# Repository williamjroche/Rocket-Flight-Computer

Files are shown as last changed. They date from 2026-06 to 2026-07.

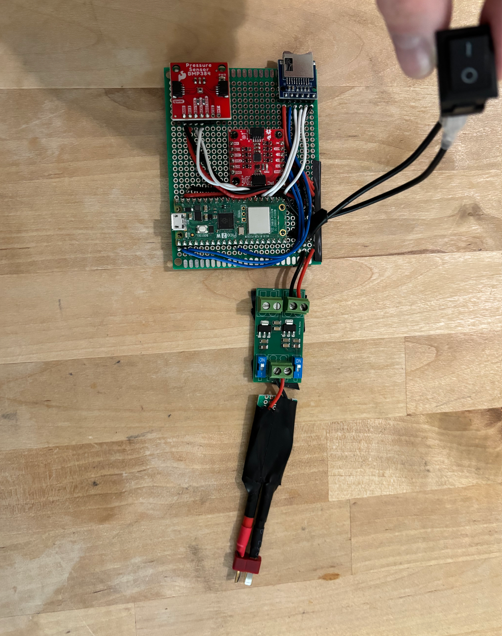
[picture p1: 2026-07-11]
prototype_pictures/photo3.png

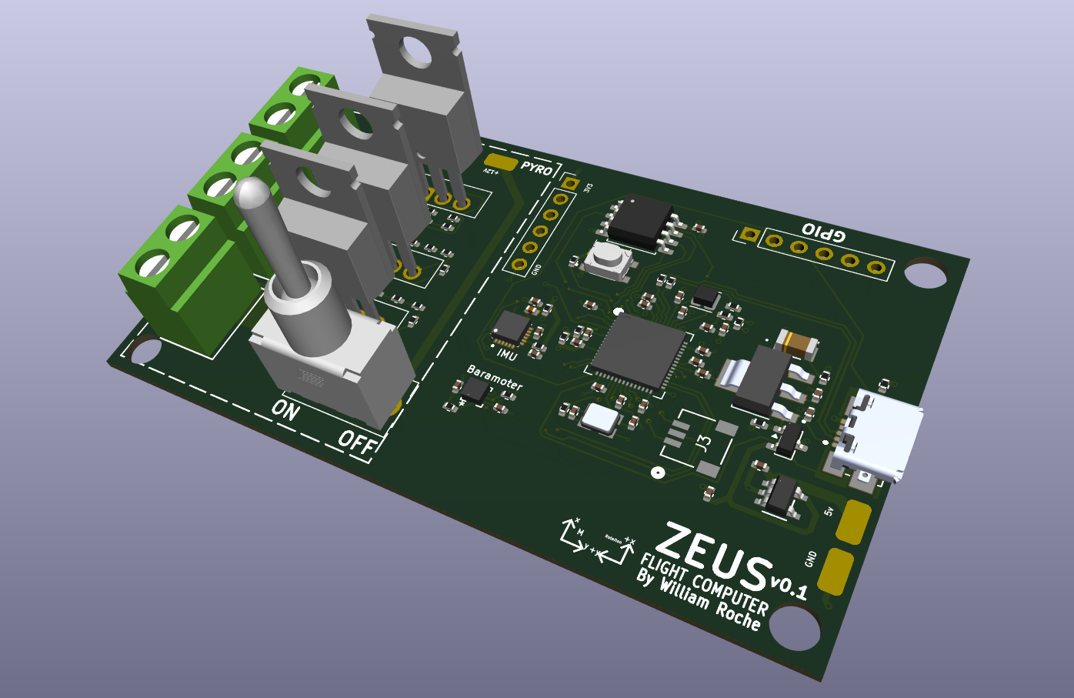
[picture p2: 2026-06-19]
PCB Photos/zeus_3d.png

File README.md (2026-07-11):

# Zeus Flight Computer

Custom flight computer for amature rockets, code named Zeus. This FC records flight data, detects apogee using a 9-axis IMU + baraomter sensor, has a built in pyro circut for firing e-matches (parachute, stage seperation, etc.).

## Project Status

- PCB design in the works, based on my Atlas Flight Controller from this project: https://github.com/williamjroche/Autonomous_drone
- Prototyping in progress on protoboard
- Board not yet fabricated, working on completing prototype first to test architecture

## Features

- 3 pyro channels with continuity sensing
- IMU + barometer sensors for apogee detection
- microSD card reader for data logging
- Automatic USB / external battery power switching (using PMOS switching circuit)
- MicroPython firmware (adapted from drone flight controller project)

## Hardware Overview

- Check out my system diagrams: [System Drawings](./System%20Drawings)
    - Explains architecture at a top level overview
- Key components table (MCU, IMU, barometer, flash, SD, pyro MOSFETs, power management)
- Link to schematic/PCB files [Zeus_FC_PCB](./Zeus_FC_PCB)

## PCB



- Stackup summary (4-layer: signal / GND / 3.3V / signal)
- Check out other photos [PCB Photos](./PCB%20Photos)
- Note: working on finding smaller SMD type IRFZ44N mosfets because these are ugly

## Protoboard Prototype

- Purpose: validate firmware and circuit behavior ahead of PCB fabrication
- Hardware used (Pico 2W, IMU breakout (ICM-20948), barometer breakout (BPM 384), microSD breakout, custom designed and fabricated 12v to 3.3v regulator board)
- Photos coming soon

## Firmware

- project specific firmware not yet developed, coming soon
- Firmware will be based off of Atlas FC firmware: https://github.com/williamjroche/Autonomous_drone/tree/main/flight_controller

## Wiring / Pinout

- Micro SD card reader:
  - CS – GPIO8
  - MISO – GPIO16
  - SCK – GPIO18
  - MOSI – GPIO19
- IMU Board:
  - SDA – GPIO0
  - SCL – GPIO1
- Barometer:
  - SDA: GPIO20
  - SCL: GPIO21

## Getting Started / Prototype Setup

If you want to make your own prototype, you'll need the following materials:

- protoboard, decently sized (mine is 7cm x 9cm)
- soldering iron
- solder (I recommend lead free)
- Fume extractor
- something to clean the soldering iron tip, like steel wool)
- 22awg wire
- Toggle switches (2)
- 1 3s LiPO battery
- Something to convert the 11.1v LiPO battery to 3.3v for the Pi
    - A buck converter off amazon will work
    - or you can download the files from the device I built from here: (https://github.com/williamjroche/Autonomous_drone/tree/main/dual_power_supply)
        - Can be fabricated using PCBway, JLCPCB, or any of your favorite fabricators. I ordered from PCBway.
- Raspberry Pi Pico 2W
- ICM-20948 IMU breakout
- BPM 384 barometer breakout
- Any microSD card reader breakout
- Electrical tape or hot glue
- MicroSD card
- Flux to make soldering easier
- Multimeter to test electrical connections (not needed but helpful)

## My Prototype: 



Here is a demo video of the working prototype: https://youtube.com/shorts/D4aav9IAWUg?si=ib71gM45oc4MuGbN

At the moment only the IMU is programmed, I need to work on the barometer sensor and apogee detection + saving data to micro SD card. You can see in the video I am using my custom dual power PCB I designed which is converting the 12v from the battery to a usable 3.3v for our sensors and Pico 2W. The switch you see is me prototyping a power switch.

## Safety Notes

- Be careful handling pyro charges!
      - I am not responible for any accidents.

## Acknowledgments

- Link to drone flight controller project: https://github.com/williamjroche/Autonomous_drone/tree/main
    - Dual Power Supply PCB is the 12v to 3.3v converter I am using on this project. The explaination under this other repo readme will help clear up any   confusion.

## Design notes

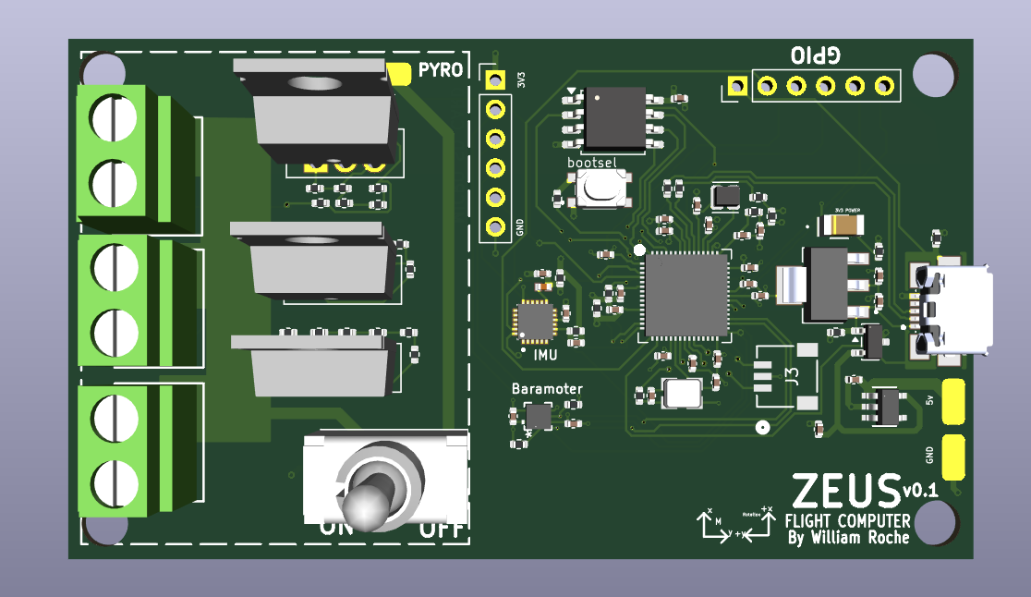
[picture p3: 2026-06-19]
PCB Photos/zeus_3d_top.png

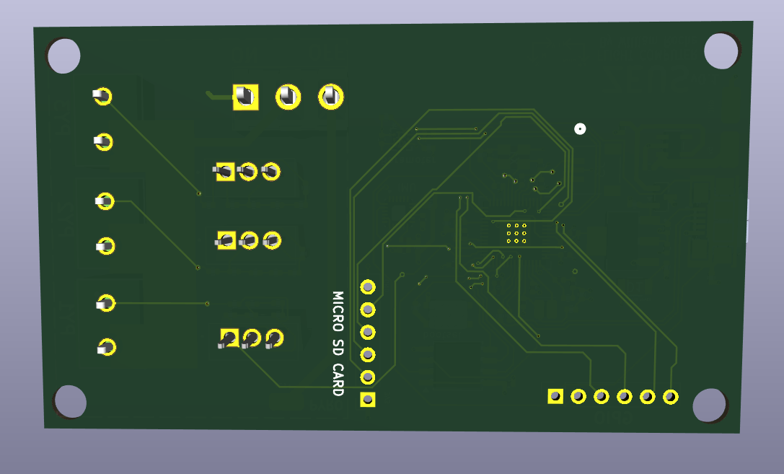
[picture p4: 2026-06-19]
PCB Photos/zeus_3d_bottom.png

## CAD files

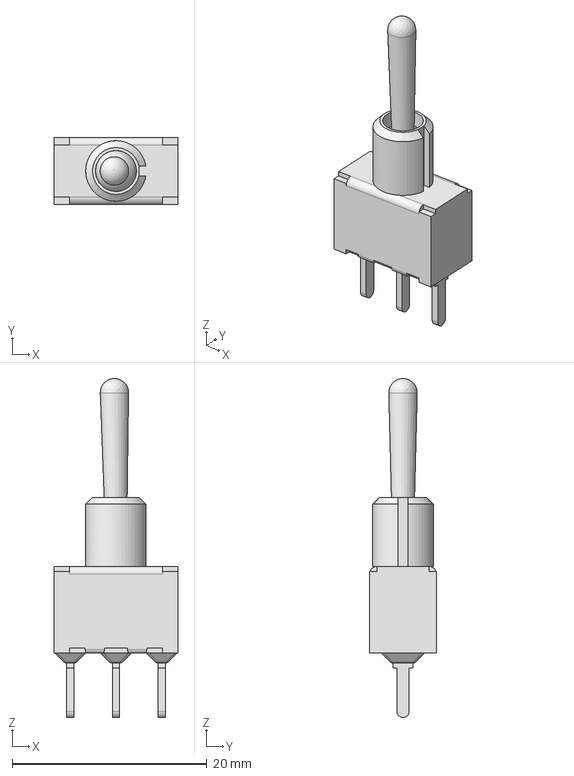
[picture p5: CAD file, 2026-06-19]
Zeus_FC_PCB/100SP1T1B4M2QE/100SP1T1B4M2QE.step
12.7 x 6.86 x 34.8 mm

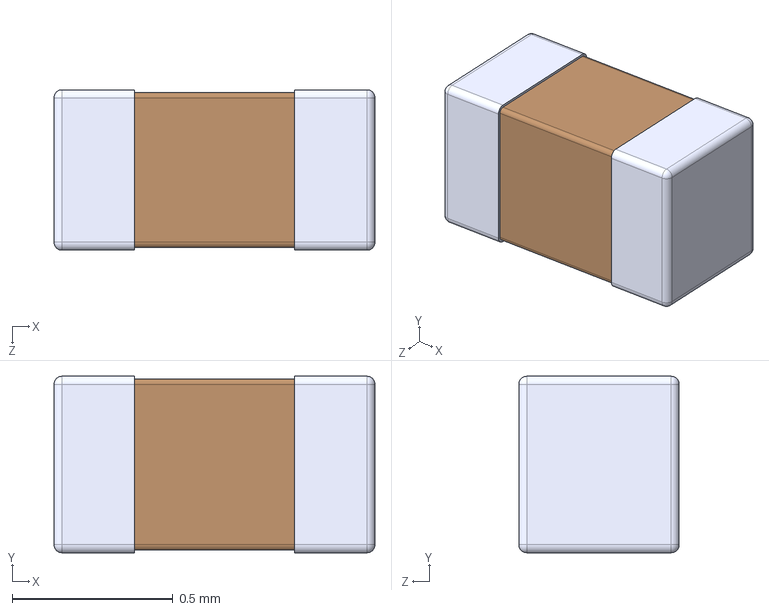
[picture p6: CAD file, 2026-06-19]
Zeus_FC_PCB/BLM15AX601SN1D/BLM15AX601SN1D.step
1.00 x 0.55 x 0.5 mm

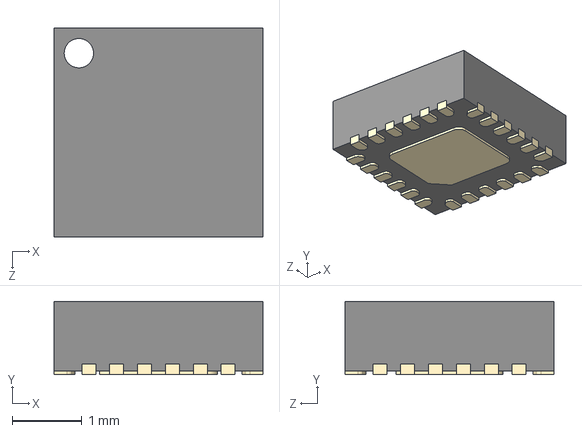
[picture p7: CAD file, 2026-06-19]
Zeus_FC_PCB/ICM-20948/ICM-20948.step
3.00 x 1.05 x 3.00 mm

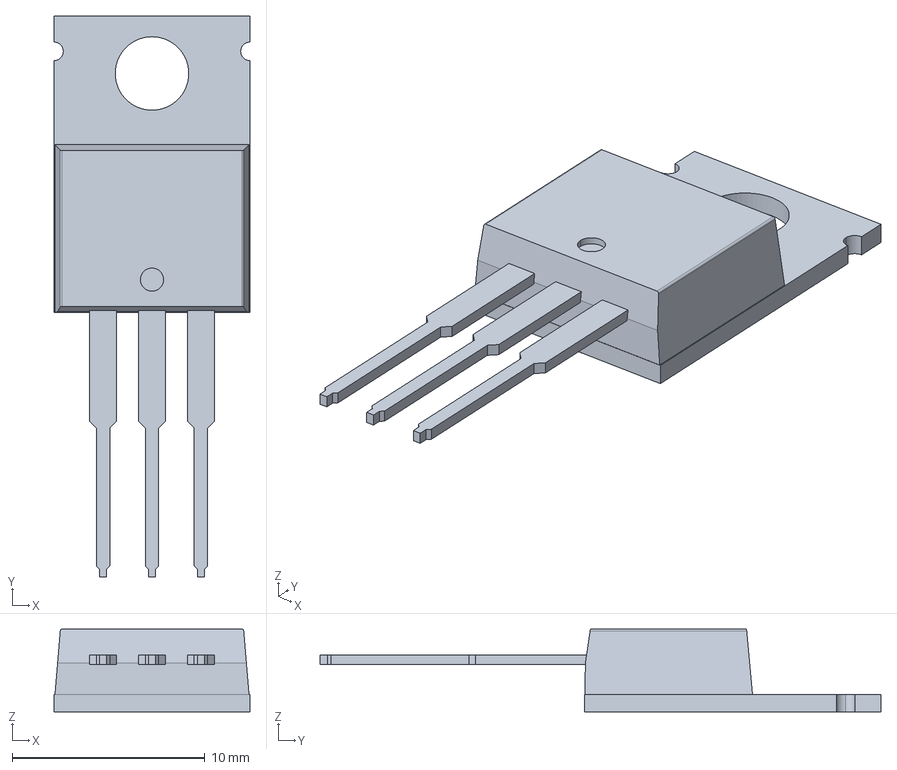
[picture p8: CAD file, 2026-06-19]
Zeus_FC_PCB/IRFZ44NPBF/irfz44npbf.stp
10.2 x 29.1 x 4.30 mm

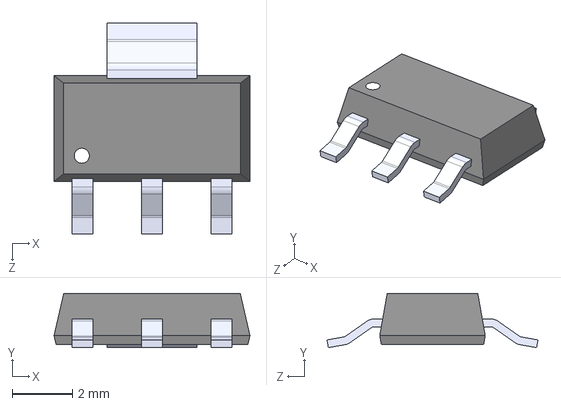
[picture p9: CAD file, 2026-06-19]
Zeus_FC_PCB/LD1117S33TR/LD1117S33TR.step
6.50 x 1.80 x 7.00 mm

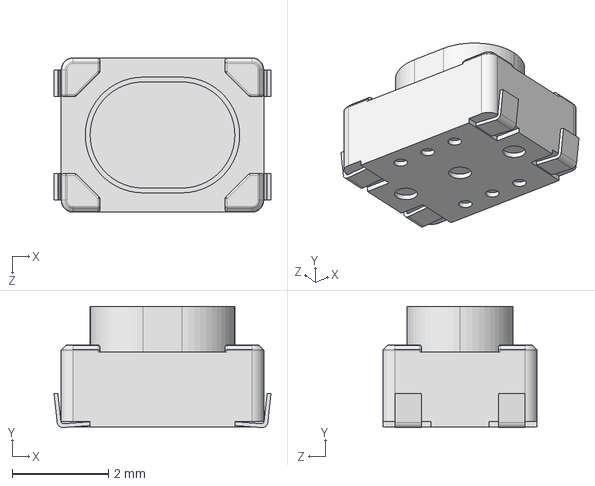
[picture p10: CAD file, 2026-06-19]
Zeus_FC_PCB/TL3365AF180QG/TL3365AF180QG.step
4.50 x 2.51 x 3.20 mm

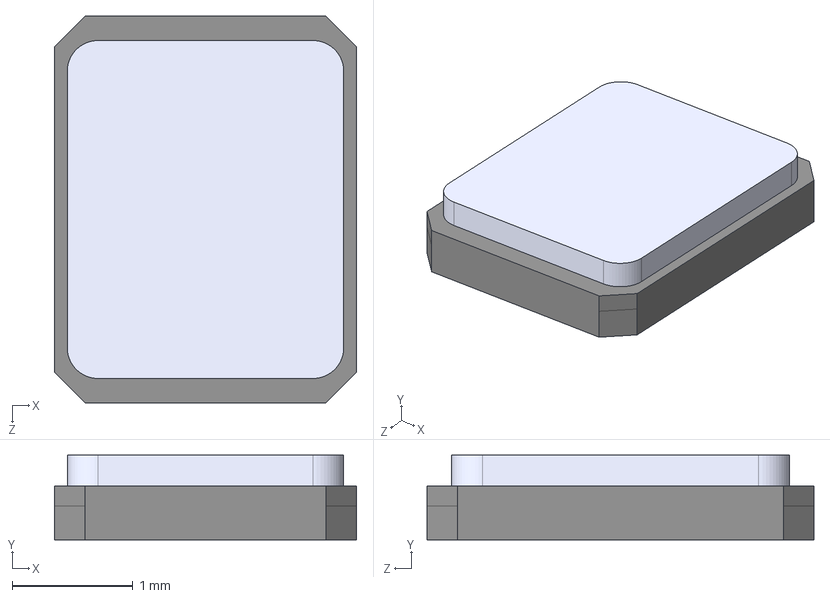
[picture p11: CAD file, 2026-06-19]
Zeus_FC_PCB/ul_ABM8-272-T3/ABM8-272-T3.STEP
2.50 x 0.7 x 3.20 mm

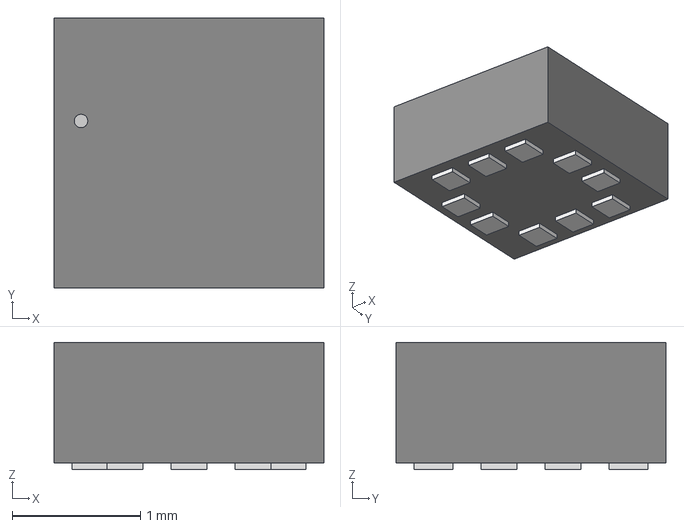
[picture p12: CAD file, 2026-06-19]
Zeus_FC_PCB/ul_BMP384/LGA10_2_0X2_0X0_95_BOS.step
2.11 x 2.11 x 0.993 mm

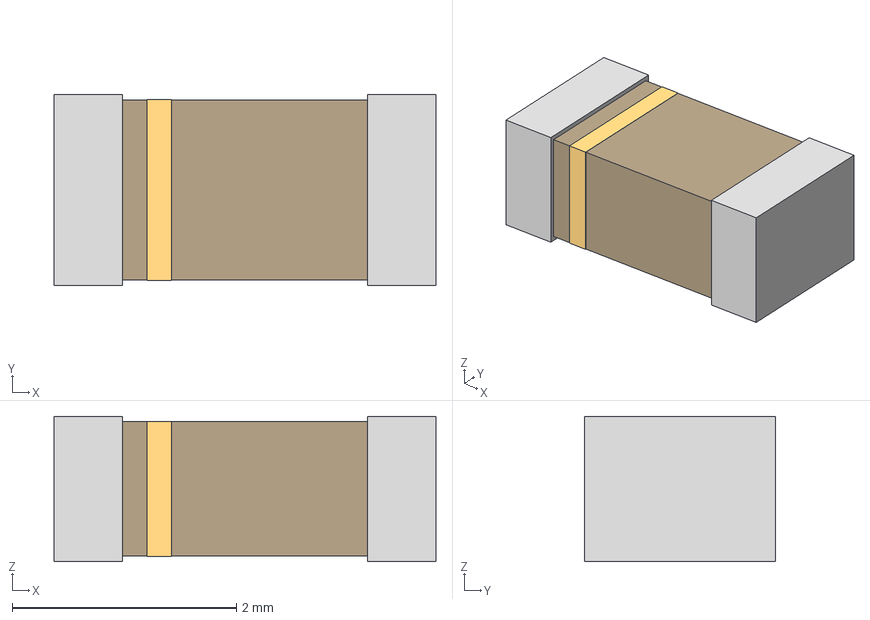
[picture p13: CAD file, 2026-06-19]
Zeus_FC_PCB/ul_CMD15-21VGD-TR8/LED_CMD15-21_VCC.step
3.40 x 1.70 x 1.29 mm

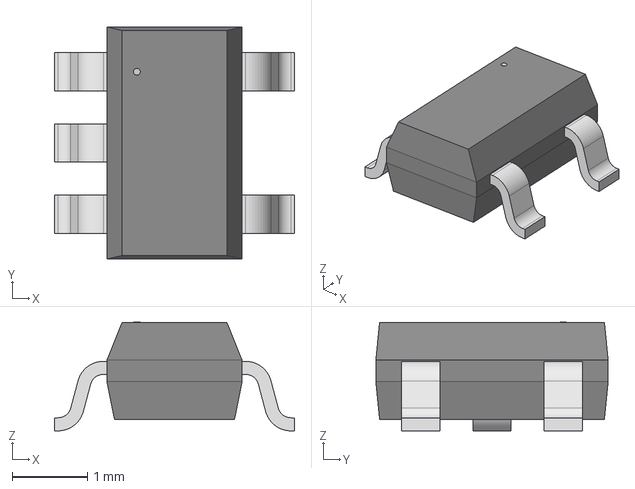
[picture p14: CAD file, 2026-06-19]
Zeus_FC_PCB/ul_MIC5504-3-3YM5-TR/KiCADv6/ul_MIC5504-3-3YM5-TR (1)/SOT-23-5_MC_MCH.step
3.20 x 3.10 x 1.45 mm

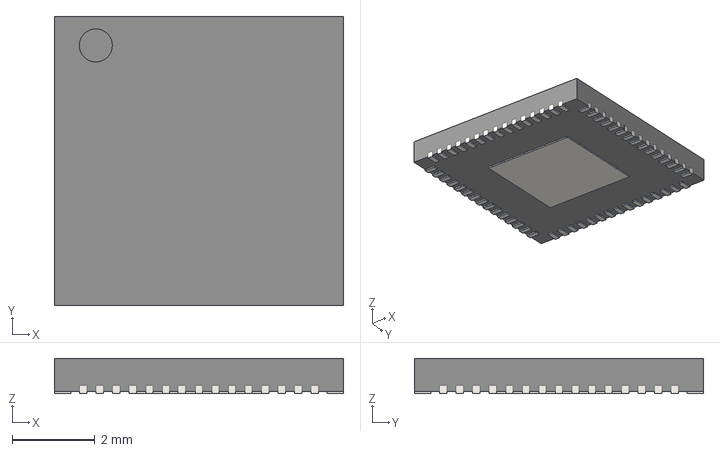
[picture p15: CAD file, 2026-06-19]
Zeus_FC_PCB/RP2350A-QFN60.step
7.00 x 7.00 x 0.85 mm

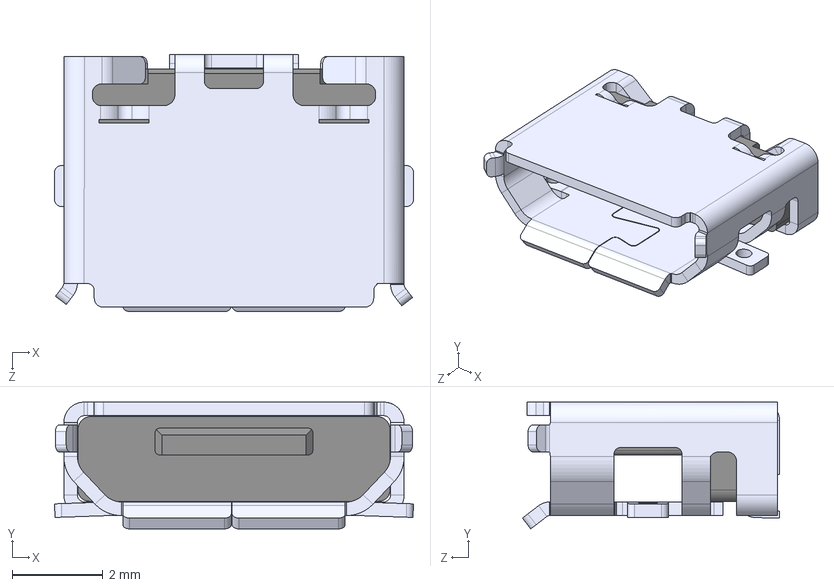
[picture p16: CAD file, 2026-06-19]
Zeus_FC_PCB/10118192-0001LF--3DModel-STEP-269445.STEP
7.91 x 2.79 x 5.67 mm

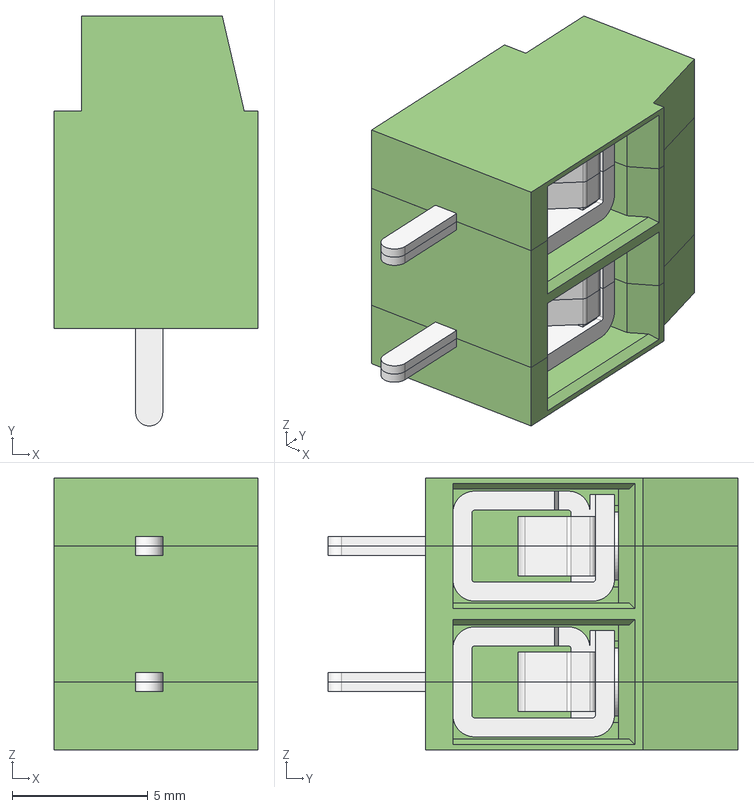
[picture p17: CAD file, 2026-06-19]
Zeus_FC_PCB/691137710002 (2)/691137710002.step
7.50 x 15.1 x 10.0 mm
MRT12P5_SX
MRT12P5_CNT
MRT12P5_DX

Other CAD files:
System Drawings/power_system_diagram.dwg
Zeus_FC_PCB/LM3940IMPX-3.3_NOPB/LM3940IMPX-3.3_NOPB.step
System Drawings/modules_system_diagram.dwg

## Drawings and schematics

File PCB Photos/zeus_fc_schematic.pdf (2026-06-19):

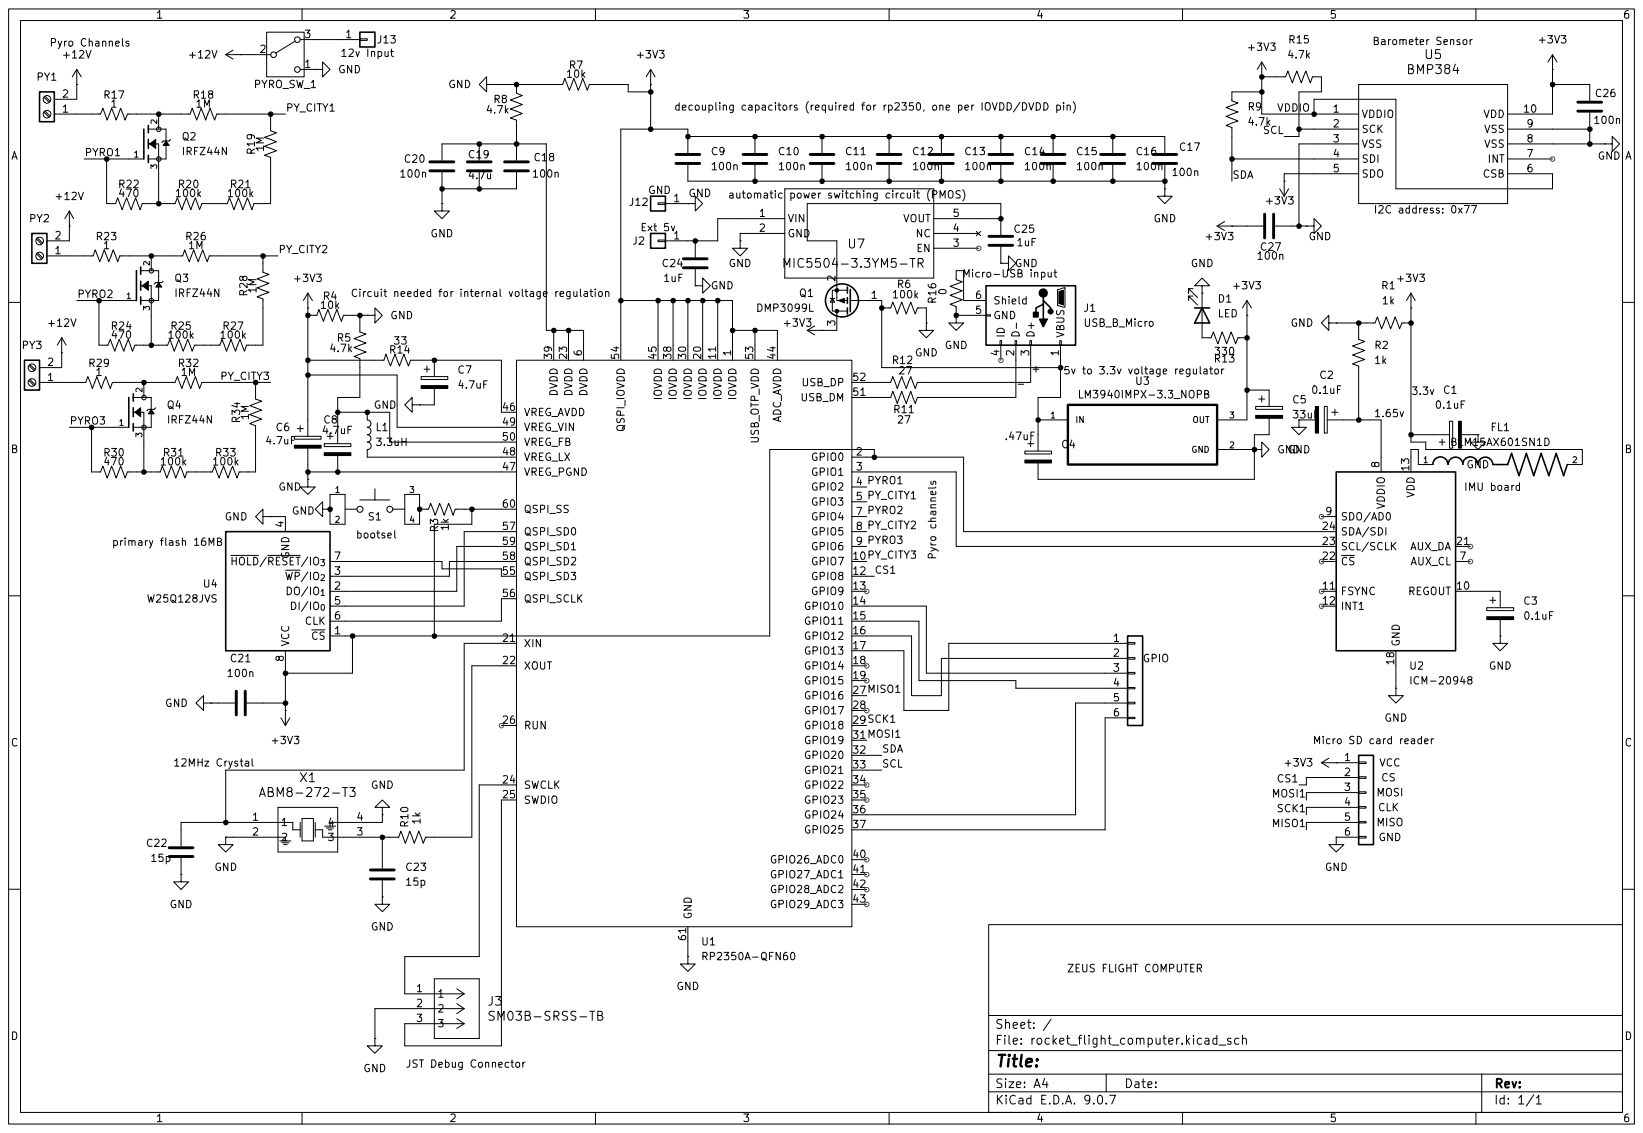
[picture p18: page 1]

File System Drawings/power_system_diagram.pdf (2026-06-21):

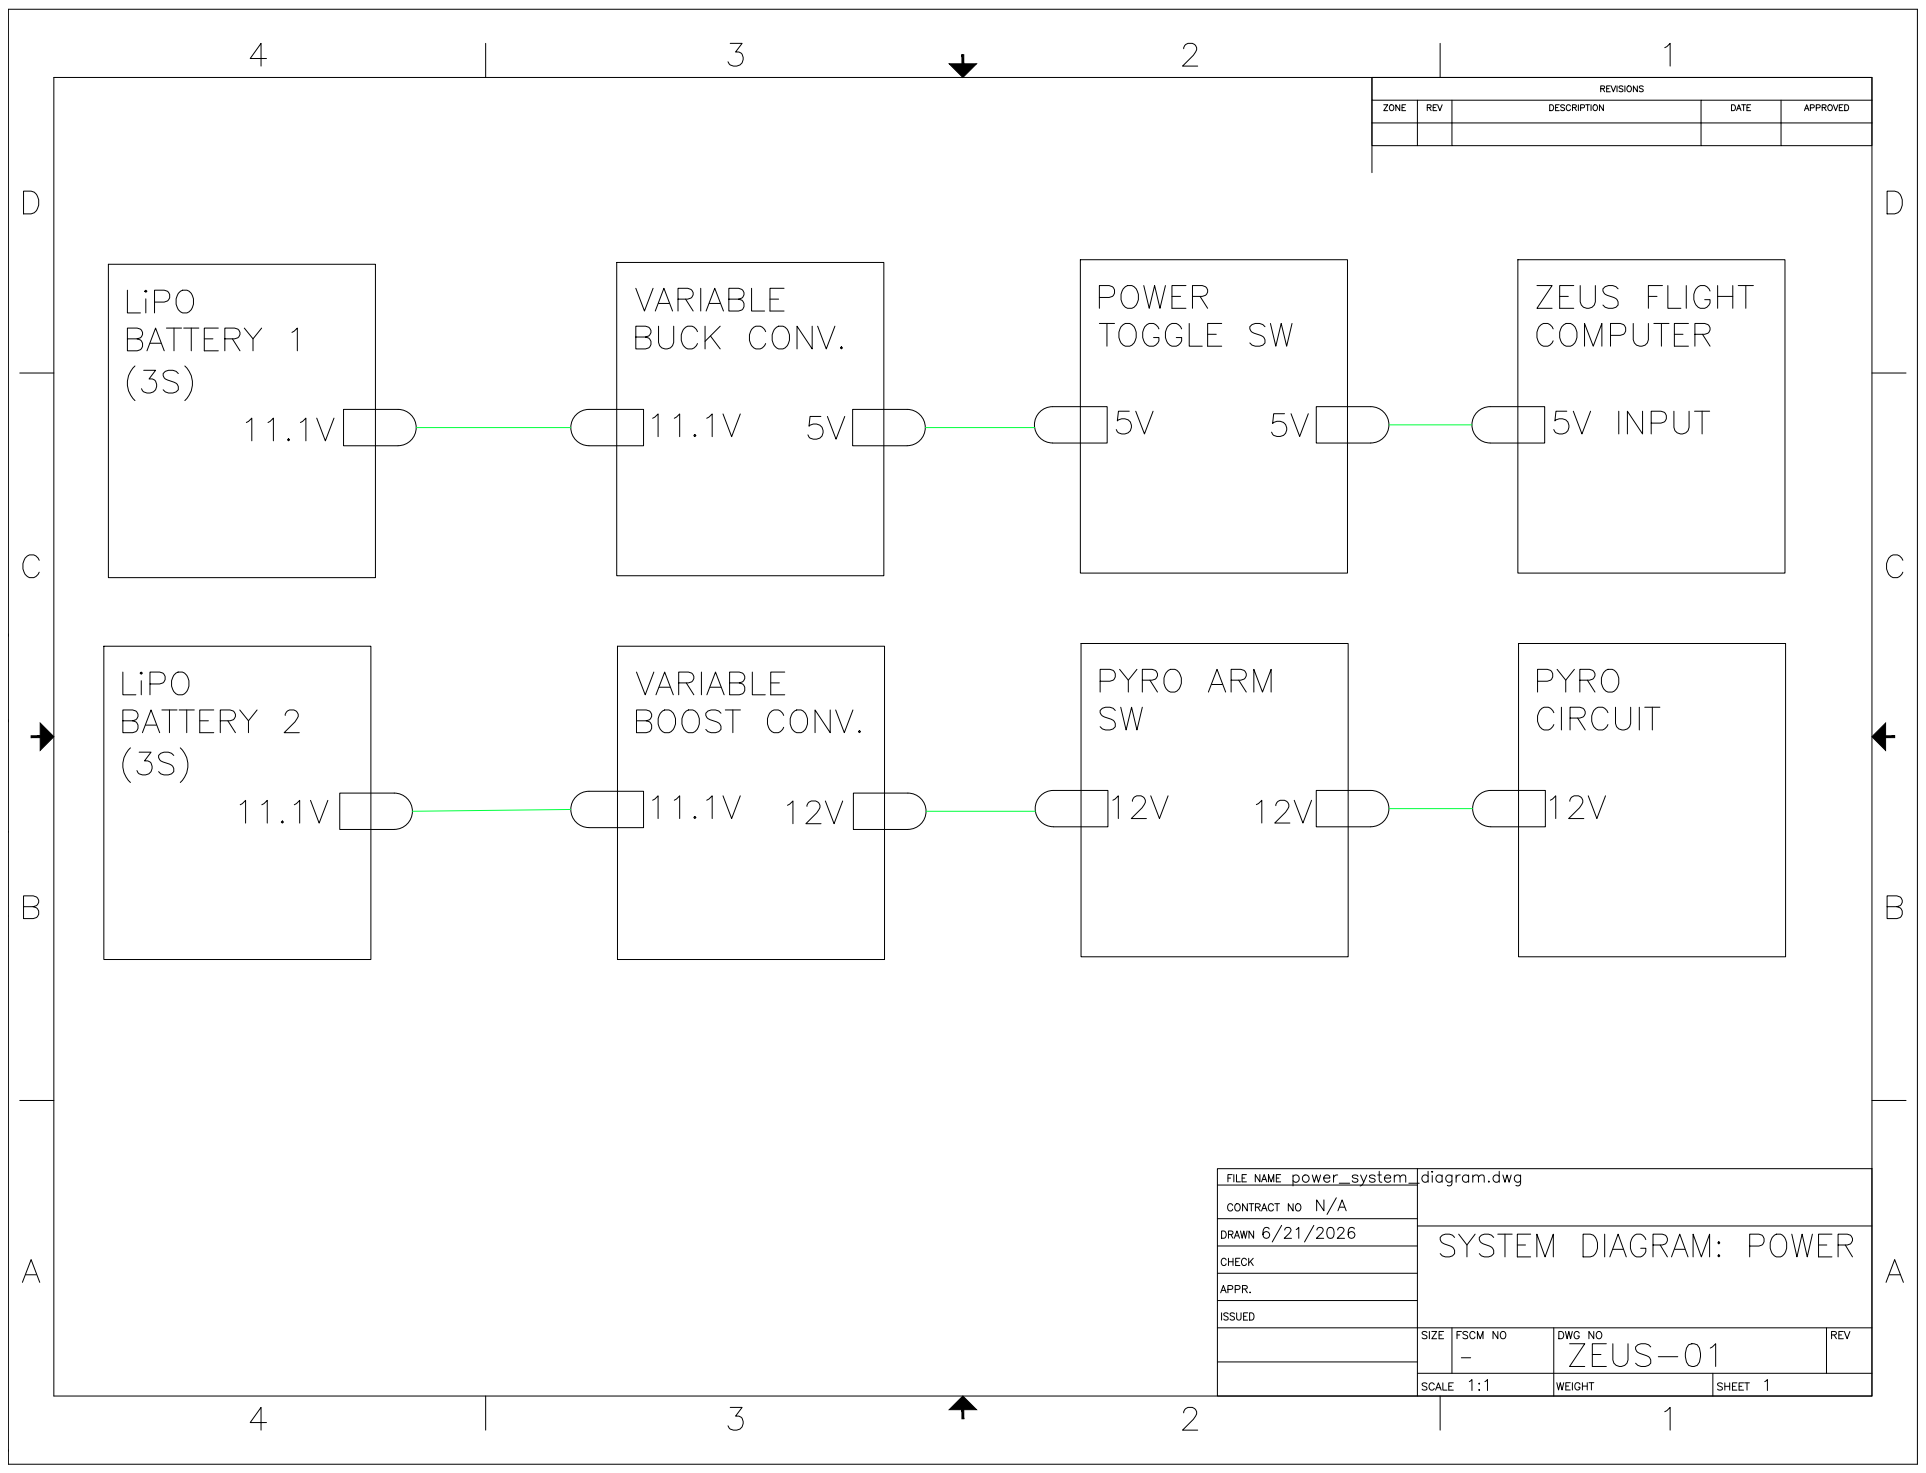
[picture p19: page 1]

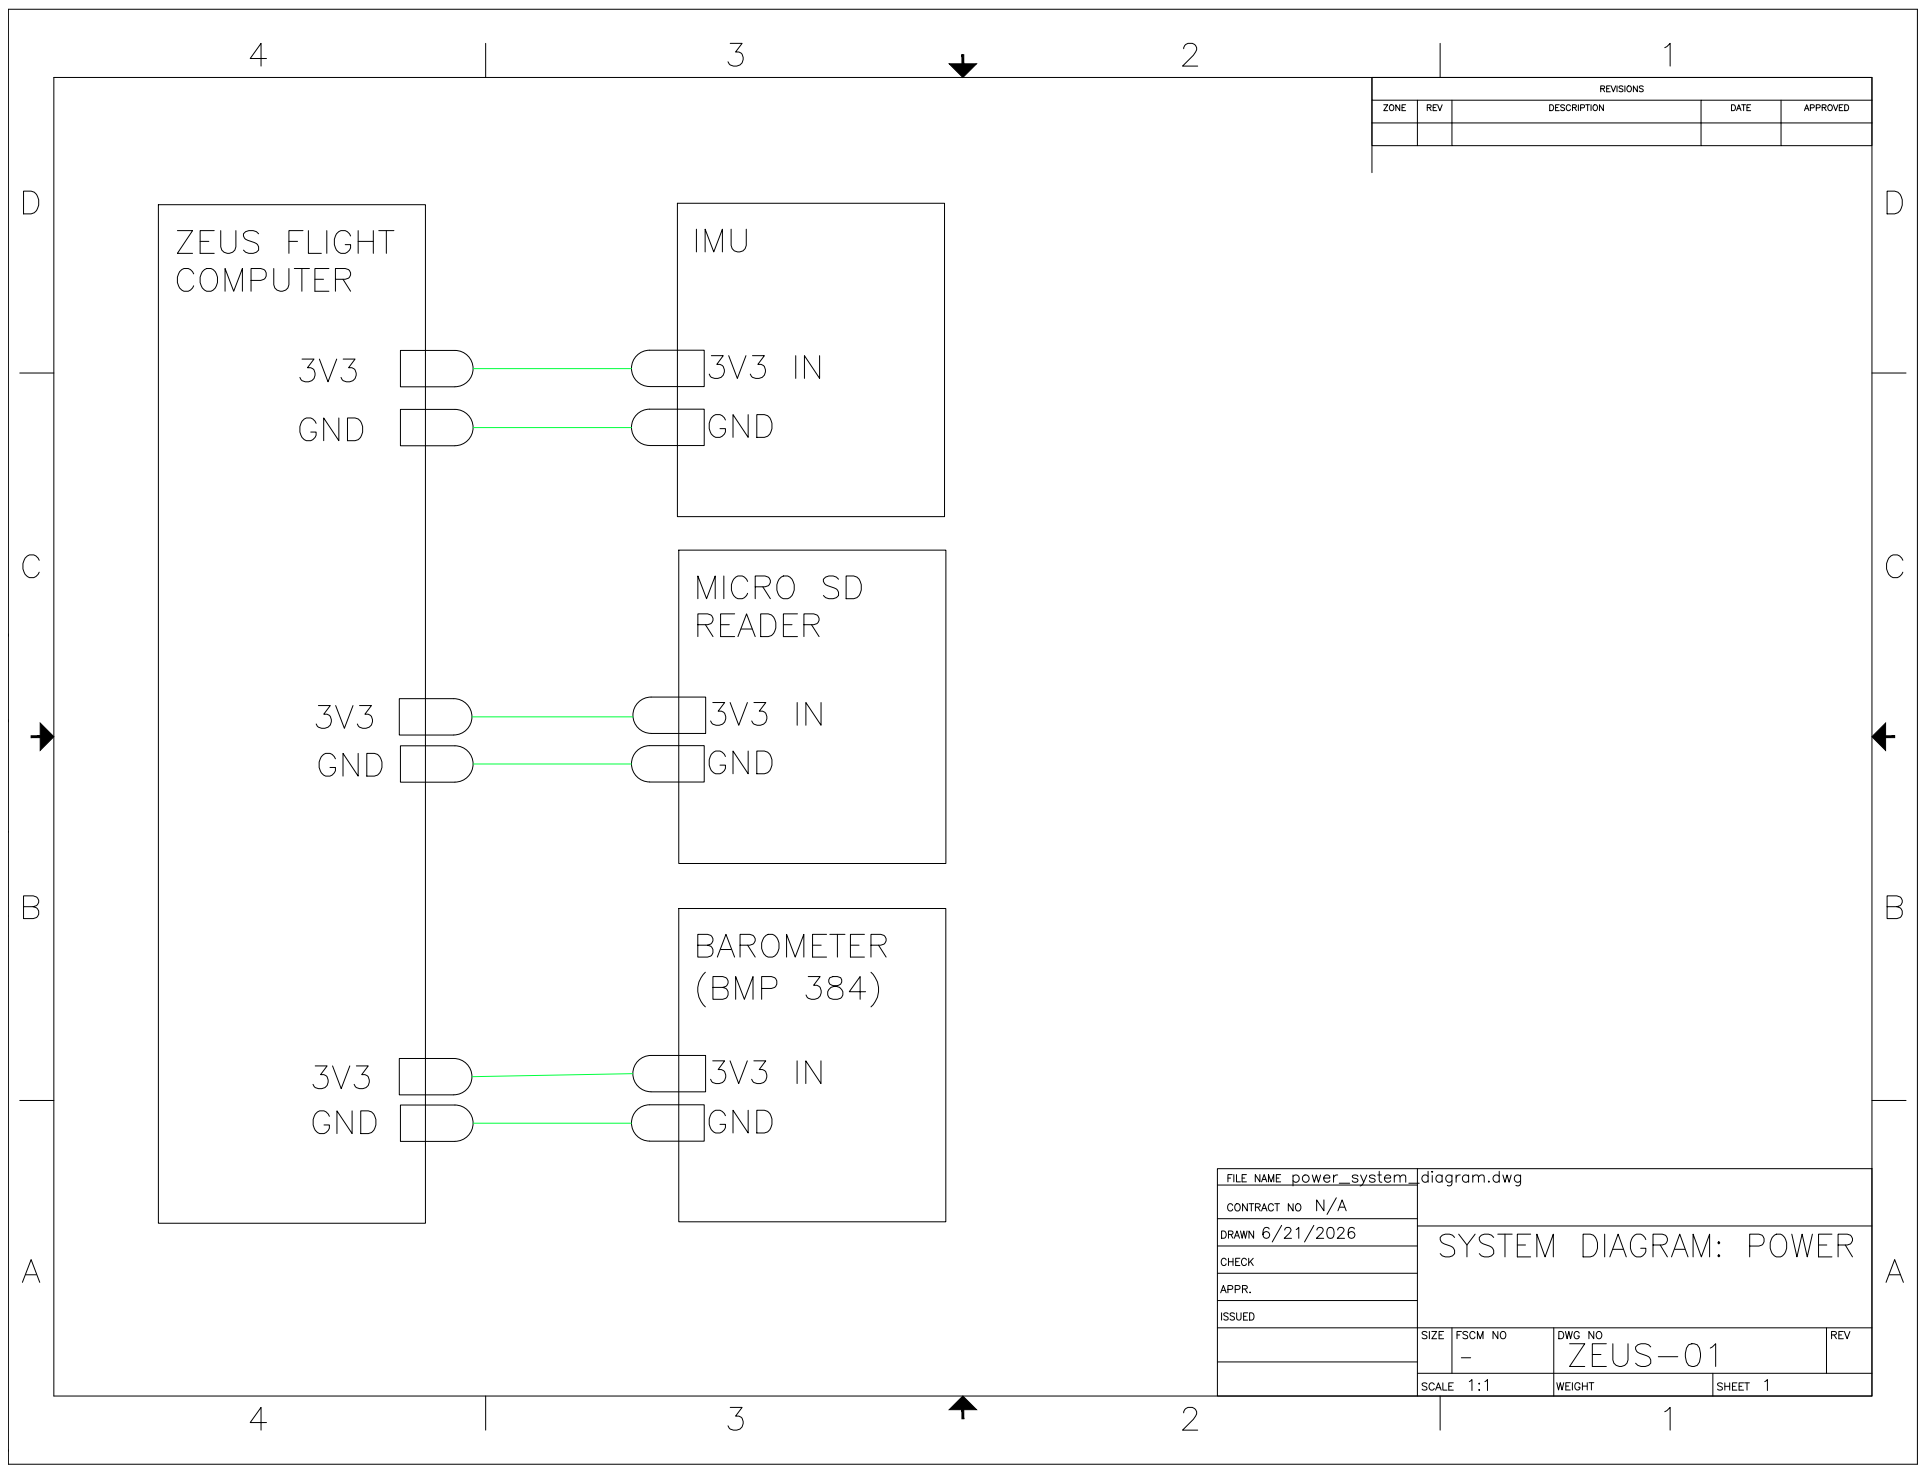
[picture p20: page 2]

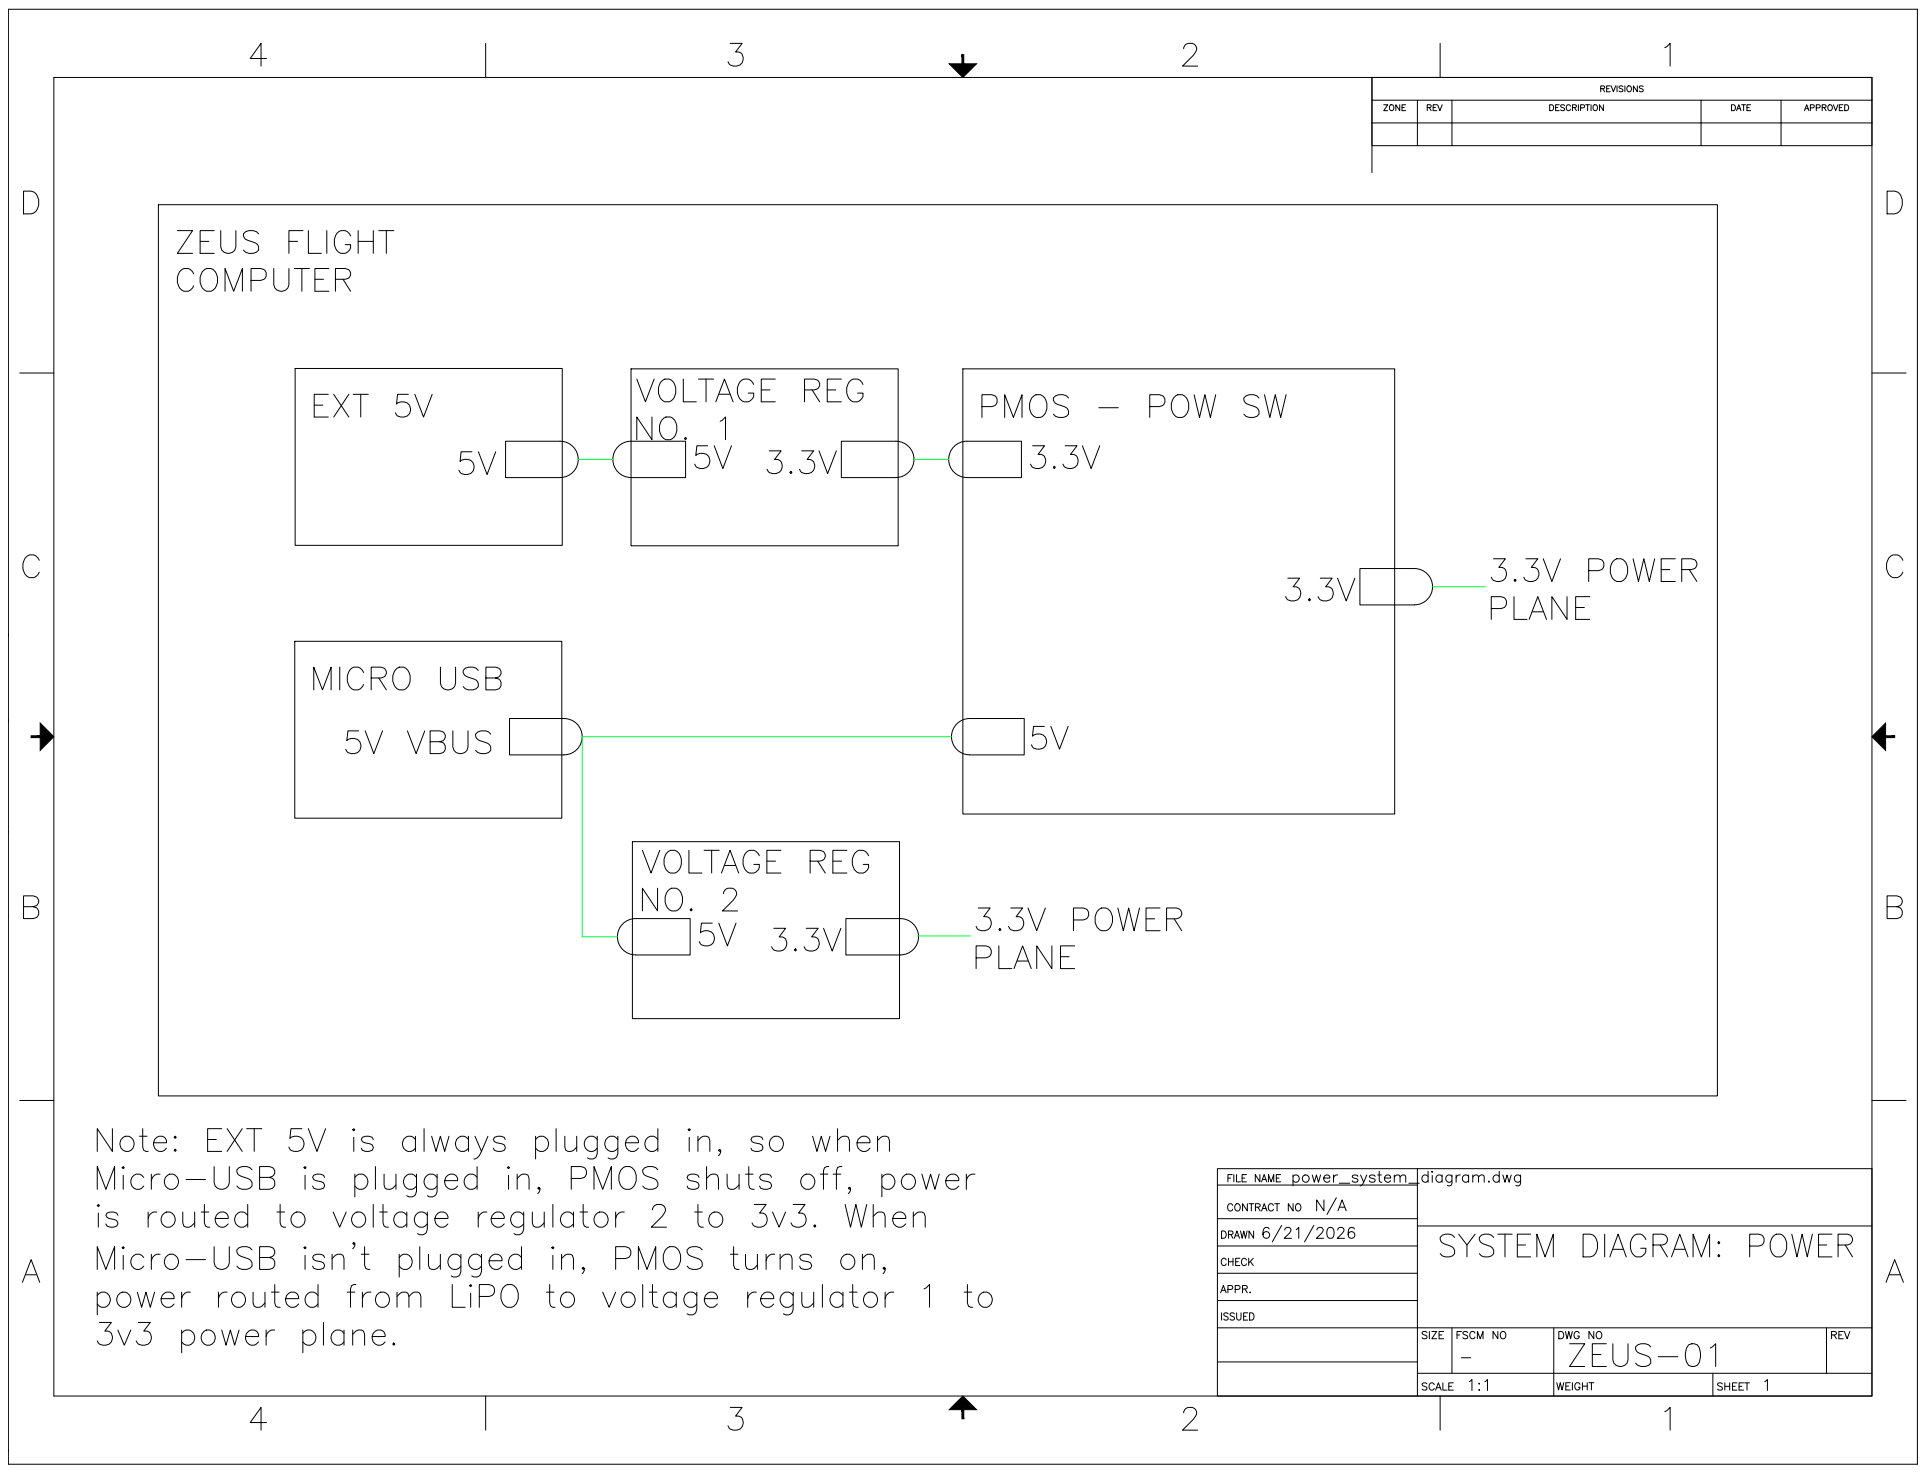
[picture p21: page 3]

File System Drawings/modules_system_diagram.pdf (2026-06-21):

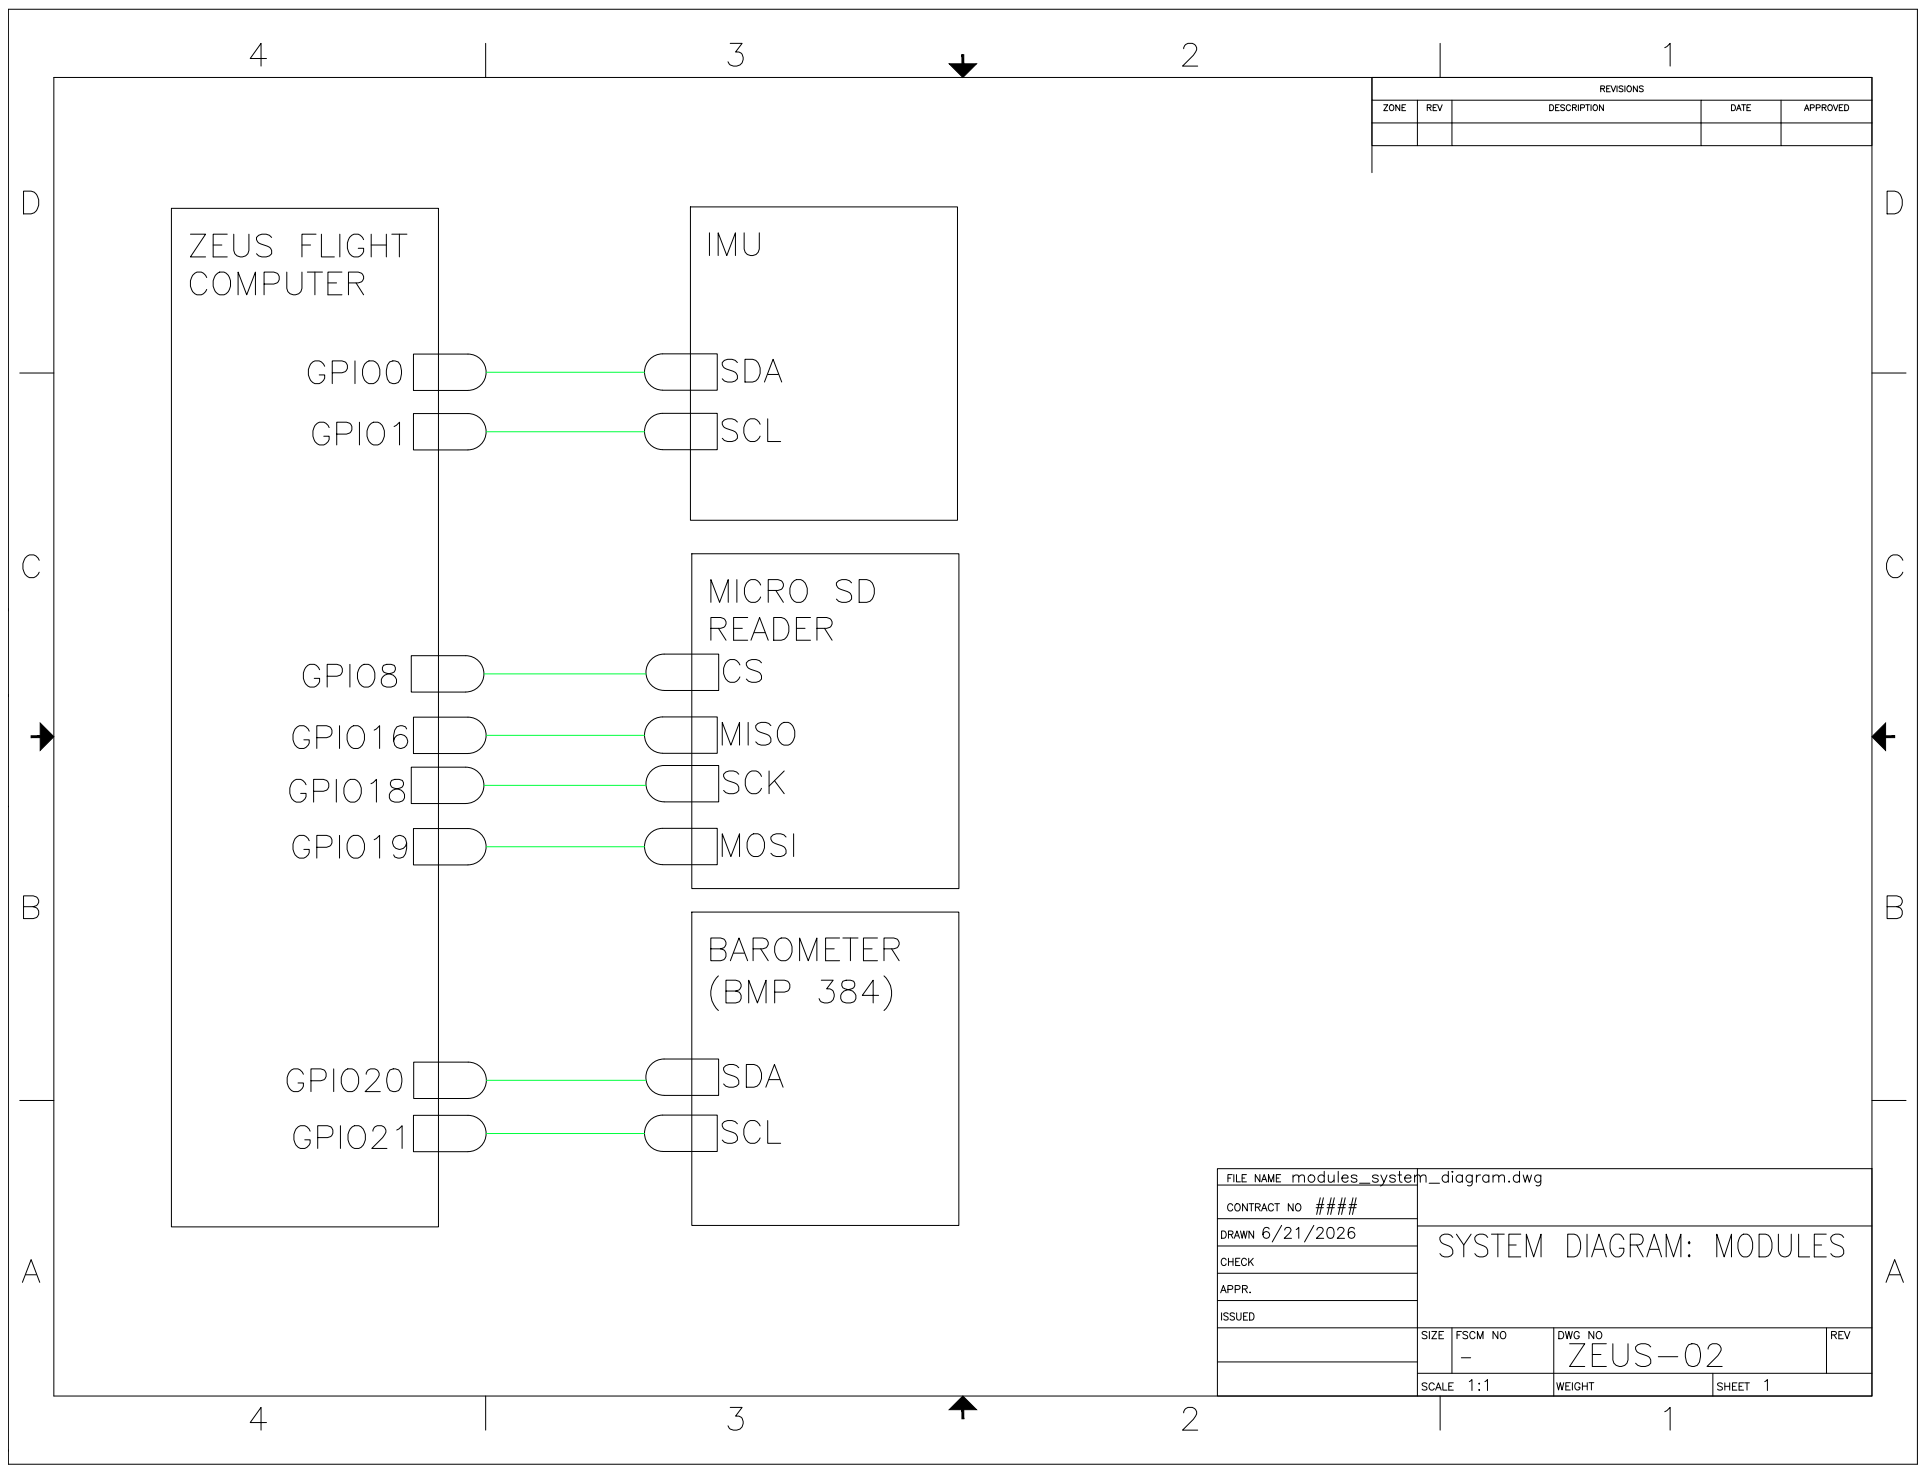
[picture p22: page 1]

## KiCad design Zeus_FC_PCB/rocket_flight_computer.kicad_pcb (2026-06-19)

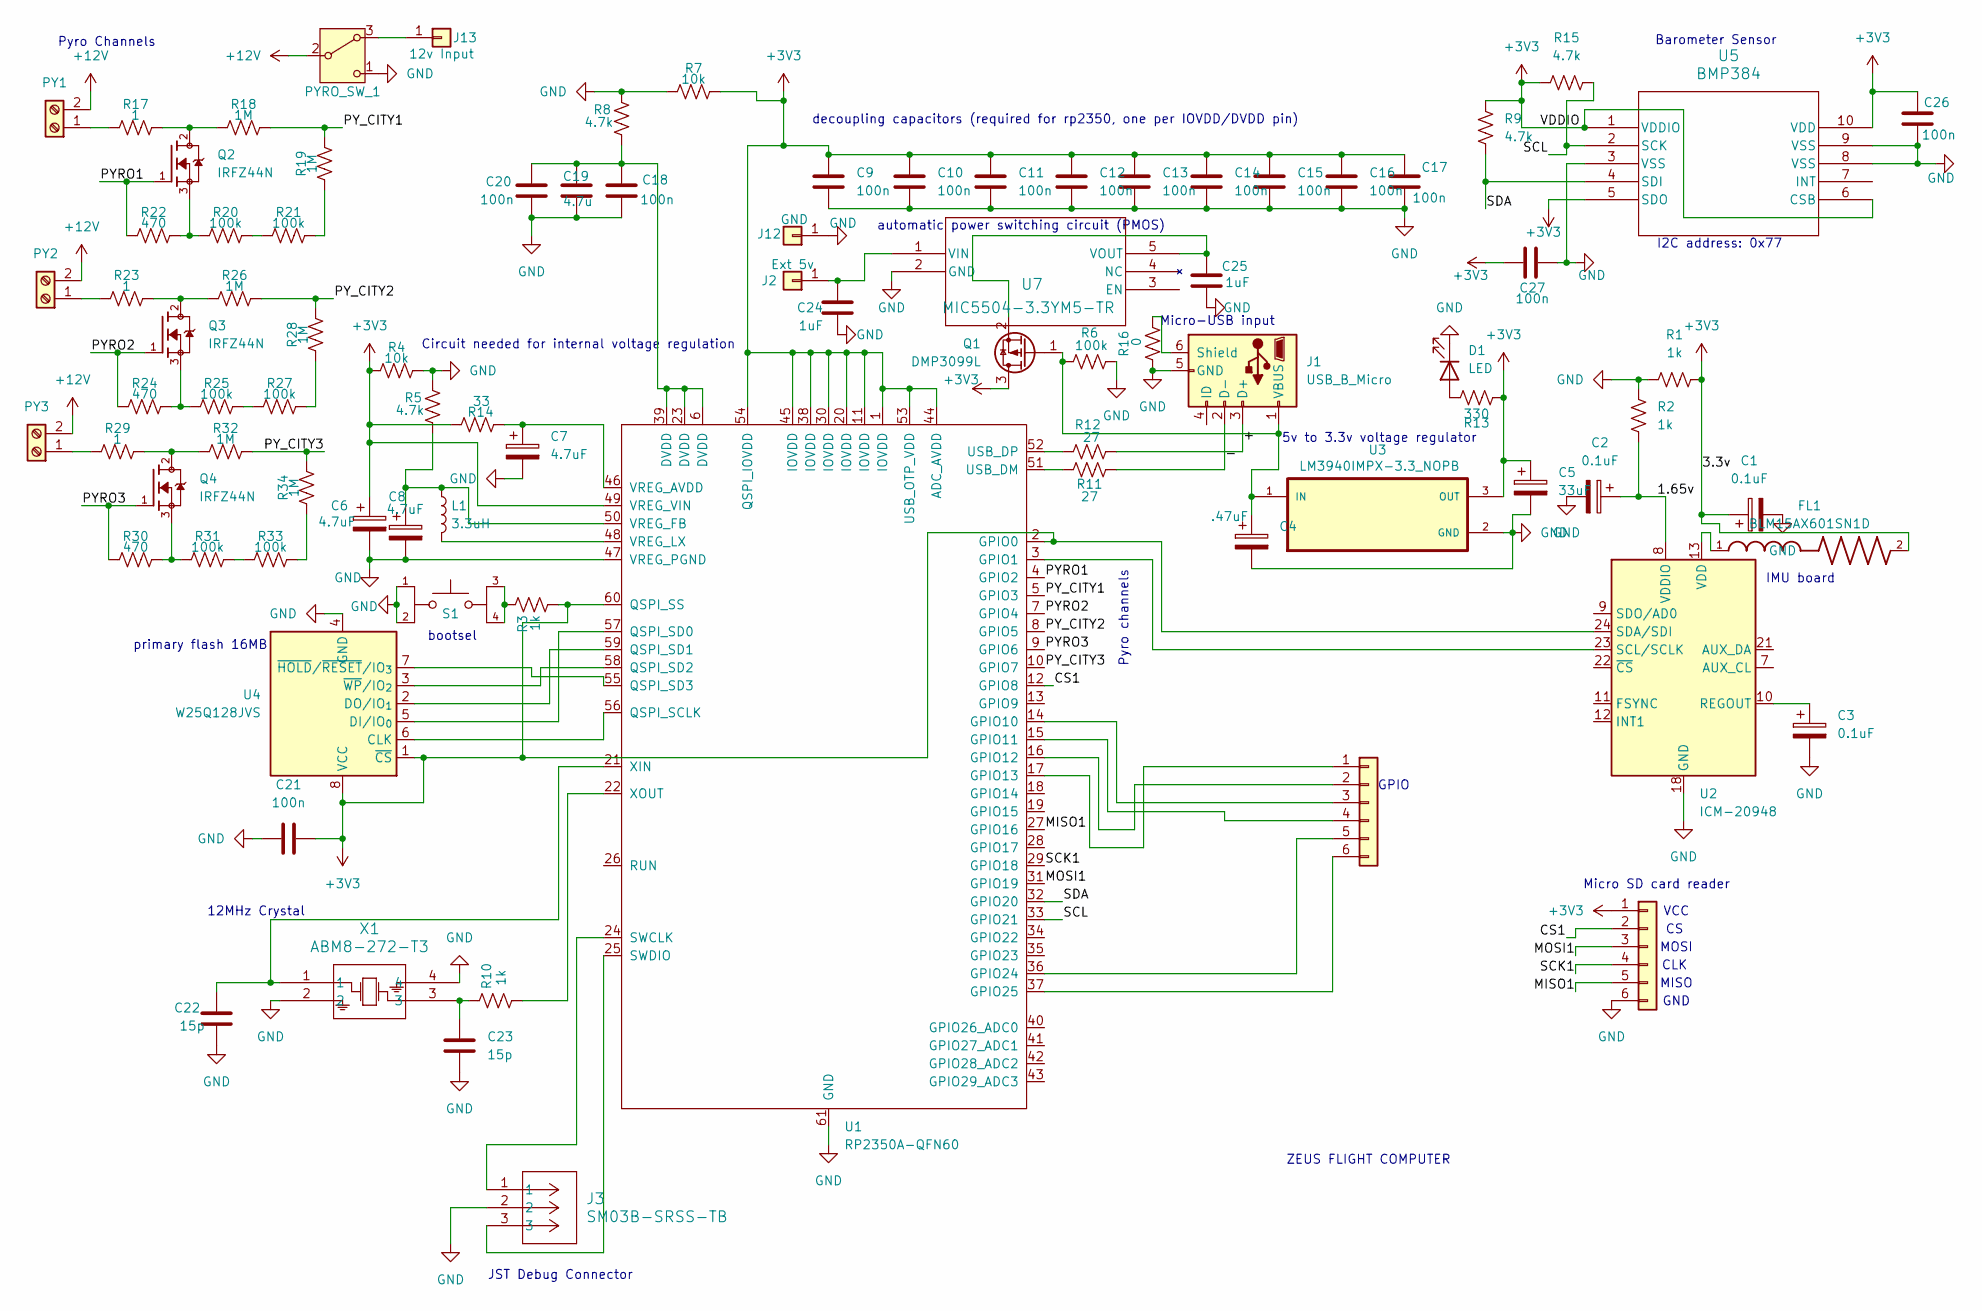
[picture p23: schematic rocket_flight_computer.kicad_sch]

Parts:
C1, C2, C3: 0.1uF; C_0402_1005Metric
C4: .47uF; C_0402_1005Metric
C5: 33uF; C_0402_1005Metric
C6, C7, C8: 4.7uF; C_0402_1005Metric
C9, C10, C11, C12, C13, C14, C15, C16, C17, C18, C20, C21, C26, C27: 100n; C_0402_1005Metric
C19: 4.7u; C_0402_1005Metric
C22, C23: 15p; C_0402_1005Metric
C24, C25: 1uF; C_0402_1005Metric
D1: LED; LED_CMD15-21_VCC
FL1: BLM15AX601SN1D; BEADC1005X55N; DigiKey_Part_Number 490-5441-1-ND
J1: USB_B_Micro; AMPHENOL_10118192-0001LF
J2: Ext 5v; SolderWirePad_1x01_SMD_2x4mm
J3: SM03B-SRSS-TB; CONN_SM03B-SRSS-TB_JST
J4, J6: Conn_01x06; PinHeader_1x06_P2.54mm_Vertical
J12: GND; SolderWirePad_1x01_SMD_2x4mm
J13: 12v Input; SolderWirePad_1x01_SMD_2x4mm
L1: 3.3uH; L_Cenker_CKCS201610
PY1, PY2, PY3: Screw_Terminal_01x02; 691137710002
PYRO_SW_1: SW_Nidec_CAS-120A1; SW_100SP1T1B4M2QE
Q1: DMP3099L; SOT-23
Q2, Q3, Q4: IRFZ44N; TO254P1016X419X2286-3; PARTREV 09/21/10
R1, R2, R3, R10: 1k; R_0402_1005Metric
R4, R7: 10k; R_0402_1005Metric
R5, R8, R9, R15: 4.7k; R_0402_1005Metric
R6, R20, R21, R25, R27, R31, R33: 100k; R_0402_1005Metric
R11, R12: 27; R_0402_1005Metric
R13: 330; R_0402_1005Metric
R14: 33; R_0402_1005Metric
R16: 0; R_0402_1005Metric
R17, R23, R29: 1; R_0402_1005Metric
R18, R19, R26, R28, R32, R34: 1M; R_0402_1005Metric
R22, R24, R30: 470; R_0402_1005Metric
S1: TL3365AF180QG; SW_TL3365AF180QG; PARTREV A; DigiKey_Part_Number EG5384CT-ND
U1: RP2350A-QFN60; RP2350A_QFN-60_EP_7.75x7.75_Pitch0.4mm
U2: ICM-20948; QFN40P300X300X105-24N
U3: LM3940IMPX-3.3_NOPB; SOT230P700X180-4N; DigiKey_Part_Number LM3940IMPX-3.3/NOPBCT-ND
U4: W25Q128JVS; SOIC-8_5.3x5.3mm_P1.27mm
U5: BMP384; LGA10_2.0X2.0X0.95_BOS
U7: MIC5504-3.3YM5-TR; SOT-23-5_MC_MCH
X1: ABM8-272-T3; ABM8-272-T3_ABR

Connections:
+3V3: C1.1, C5.1, C6.1, C9.1, C10.1, C11.1, C12.1, C13.1, C14.1, C15.1, C16.1, C17.1, C21.1, C26.1, C27.1, FL1.2, J4.1, Q1.3 (D), R1.2, R3.1, R4.2, R7.1, R9.2, R13.2, R14.1, R15.2, U1.1 (IOVDD), U1.2 (GPIO0), U1.11 (IOVDD), U1.20 (IOVDD), U1.30 (IOVDD), U1.38 (IOVDD), U1.44 (ADC_AVDD), U1.45 (IOVDD), U1.49 (VREG_VIN), U1.53 (USB_OTP_VDD), U1.54 (QSPI_IOVDD), U1.60 (QSPI_SS), U2.24 (SDA/SDI), U3.3 (OUT), U4.1 (~CS), U4.8 (VCC), U5.1 (VDDIO), U5.5 (SDO), U5.6 (CSB), U5.10 (VDD)
+12V: PY1.2, PY2.2, PY3.2, PYRO_SW_1.2 (B)
/1.65v: C2.1, R2.1, U2.8 (VDDIO)
/+: J1.3 (D+), R12.2
/-: J1.2 (D-), R11.2
/CS1: J4.2, U1.12 (GPIO8)
/MISO1: J4.5, U1.27 (GPIO16)
/MOSI1: J4.3, U1.31 (GPIO19)
/PYRO1: Q2.1, R22.2, U1.4 (GPIO2)
/PYRO2: Q3.1, R24.2, U1.7 (GPIO4)
/PYRO3: Q4.1, R30.2, U1.9 (GPIO6)
/PY_CITY1: R18.1, R19.1, U1.5 (GPIO3)
/PY_CITY2: R26.1, R28.1, U1.8 (GPIO5)
/PY_CITY3: R32.1, R34.1, U1.10 (GPIO7)
/SCK1: J4.4, U1.29 (GPIO18)
/SCL: R15.1, U1.33 (GPIO21), U5.2 (SCK)
/SDA: R9.1, U1.32 (GPIO20), U5.4 (SDI)
GND: C1.2, C2.2, C3.2, C4.2, C5.2, C6.2, C7.2, C8.2, C9.2, C10.2, C11.2, C12.2, C13.2, C14.2, C15.2, C16.2, C17.2, C18.2, C19.2, C20.2, C21.2, C22.2, C23.2, C24.2, C25.2, C26.2, C27.2, D1.1 (K), J1.5 (GND), J3.2, J4.6, J12.1, PYRO_SW_1.1 (C), R1.1, R2.2, R4.1, R5.2, R6.2, R7.2, R8.2, R16.1, S1.1, S1.2, U1.47 (VREG_PGND), U1.61 (GND), U2.18 (GND), U2.20 (GND), U3.2 (GND), U3.4 (GND), U4.4 (GND), U5.3 (VSS), U5.8 (VSS), U5.9 (VSS), U7.2 (GND), X1.2, X1.4
unnamed: C18.1, C19.1, C20.1, R8.1, U1.6 (DVDD), U1.23 (DVDD), U1.39 (DVDD)
unnamed: C23.1, R10.2, X1.3
unnamed: D1.2 (A), R13.1
unnamed: J1.6 (Shield), R16.2
unnamed: C4.1, J1.1 (VBUS), Q1.1 (G), R6.1, U3.1 (IN)
unnamed: C24.1, J2.1, U7.1 (VIN)
unnamed: J6.1, U1.17 (GPIO13)
unnamed: J6.2, U1.16 (GPIO12)
unnamed: J6.3, U1.14 (GPIO10)
unnamed: J6.4, U1.15 (GPIO11)
unnamed: J6.5, U1.36 (GPIO24)
unnamed: J6.6, U1.37 (GPIO25)
unnamed: J13.1, PYRO_SW_1.3 (A)
unnamed: PY1.1, R17.2
unnamed: PY2.1, R23.2
unnamed: PY3.1, R29.2
unnamed: C25.1, Q1.2 (S), U7.5 (VOUT)
unnamed: Q2.2, R17.1, R18.2
unnamed: Q2.3, R20.2, R22.1
unnamed: Q3.2, R23.1, R26.2
unnamed: Q3.3, R24.1, R25.2
unnamed: Q4.2, R29.1, R32.2
unnamed: Q4.3, R30.1, R31.2
unnamed: R3.2, S1.3, S1.4
unnamed: R19.2, R21.1
unnamed: R20.1, R21.2
unnamed: R25.1, R27.2
unnamed: R27.1, R28.2
unnamed: R31.1, R33.2
unnamed: R33.1, R34.2
unnamed: U1.3 (GPIO1), U2.23 (SCL/SCLK)
unnamed: U1.56 (QSPI_SCLK), U4.6 (CLK)
unnamed: U1.57 (QSPI_SD0), U4.5 (DI/IO_{0})
unnamed: U1.59 (QSPI_SD1), U4.2 (DO/IO_{1})
unnamed: U1.58 (QSPI_SD2), U4.3 (~WP/IO_{2})
unnamed: U1.55 (QSPI_SD3), U4.7 (~HOLD/~RESET/IO_{3})
unnamed: J3.1, U1.24 (SWCLK)
unnamed: J3.3, U1.25 (SWDIO)
unnamed: R11.1, U1.51 (USB_DM)
unnamed: R12.1, U1.52 (USB_DP)
unnamed: C7.1, R14.2, U1.46 (VREG_AVDD)
unnamed: C8.1, L1.1, R5.1, U1.50 (VREG_FB)
unnamed: L1.2, U1.48 (VREG_LX)
unnamed: C22.1, U1.21 (XIN), X1.1
unnamed: R10.1, U1.22 (XOUT)
unnamed: C3.1, U2.10 (REGOUT)
unnamed: FL1.1, U2.13 (VDD)

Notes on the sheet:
5v to 3.3v voltage regulator
GND
I2C address: 0x77
JST Debug Connector
Barometer Sensor
primary flash 16MB
12MHz Crystal
automatic power switching circuit (PMOS)
CLK
Micro-USB input
IMU board
Pyro Channels
MISO
decoupling capacitors (required for rp2350, one per IOVDD/DVDD pin)
Circuit needed for internal voltage regulation
VCC
bootsel
GPIO
ZEUS FLIGHT COMPUTER
MOSI
Pyro channels
Micro SD card reader

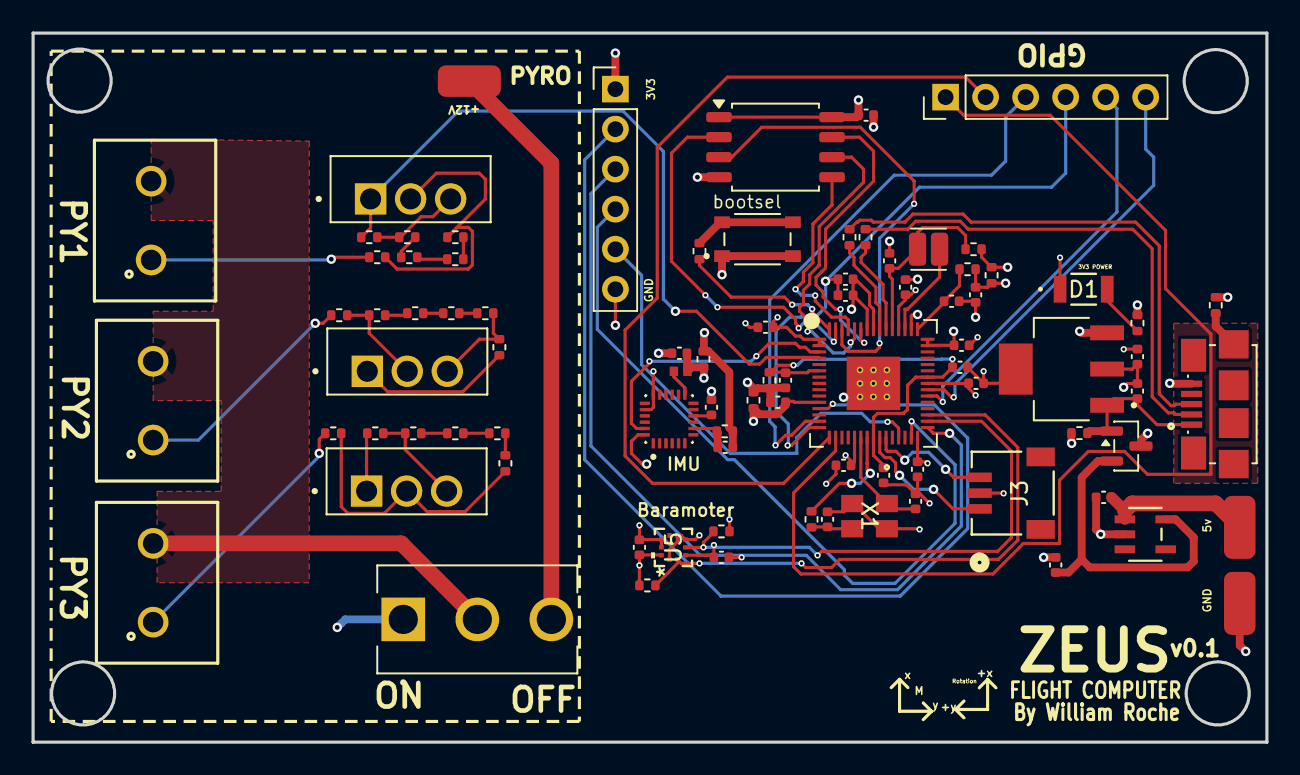
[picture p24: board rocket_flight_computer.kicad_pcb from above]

Board: 4 copper layers, 78.3 x 45.0 mm, 87 parts (0 on the bottom side), 64 nets.
